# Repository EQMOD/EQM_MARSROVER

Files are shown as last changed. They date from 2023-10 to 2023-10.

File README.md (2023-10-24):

# EQM_MARSROVER
A 3d printed Mars Rover with DUAL Arduino Electronics

A 3D Printed Perseverance Mars Rover of NASA with dual Arduino Electronics.  The first Arduino a NANO, manages all 6 motors (speed and direction) of the 6-Wheel Rover where each wheel is independently controllable using the Arduino Servo libary. The motor speed controller uses the SG90 Servo board including the feedback potentiometer as an Electronic Speed Controller for each of the 6 wheels. Four more servo boards are added to manage the steering process performed on  all four corner wheels. So thats 6+4 SG90 Servo boards, 6 acting as Motor ESC and 4 as wheel steering. A 2nd BLE-33 Sense NANO Arduino with a TENSORFLOW AI/ML embedded engine  is used to process sensor data (built-in sensors within the Arduino, LIDARS, PIXYCAM, and MPU Gyro Sensor) The BLE-33 Sens NANO communicates with the 1st NANO Arduino via I2c. The entire platform is 3D-Printed with STL files downloaded from the NASA Website/GITHUB and were modified to accomodate the electronics and motors/servos. 

https://github.com/nasa/NASA-3D-Resources/tree/master/3D%20Models/M2020-Model-Rover-STLs512020



Rover Electronics mounted on the chassis box;



Sensor/Device List as implemented on the Arduino Codes;

"A TENSORFLOW AI/ML embedded module, 6 individually addressable bidirectional motors for all 6 Wheels, 4 LIDAR Sensors: two for the front two wheels, 1 at the rear wheel, 1 on the head mast, A CMU Pixy Camera mounted in front of the Rover, A streaming camera on the Main Mast accessible using wifi via a Mobile app, Dual Micro controllers in a master slave configuration,  two  6 DOF gyro/accelerometers - one on top of the differential bar, another on one on the Nano BLE Sense microcontroller, a light/color/proximity sensor on the ble sense, a barometric/temp/pressure also on the ble sense, an audio mic also on the ble sense, a couple of servos - one for the Mast, and one for the Ingenuity copter deployment, and FOUR more servos for each corner wheel, an RC module to remotely control the bot or feed it with PWM data for subroutine triggers  from the 2.4ghz transmitter , A Bluetooth module for mobile app communication..."

The platform also include a mini version of the Mars Ingenuity Helicopter to demonstrate the deployment process using a SG90 Servo to drop the model under the belly of the perseverance rover;



Ingenuity Deployment assembly  (Version 1)



Ingenuity Deployment assembly  (Version 2)



The Platform uses multiple sensors ((built-in sensors within the Arduino BLE Sense, LIDARS, PIXYCAM, and MPU Gyro Sensor) which can be used for multi-processing/interactive experiments



Below is the connection diagram of all the motors, servos, and sensors. Motor/Servo Control is distributed on the Arduino NANO (Acting as Slave) and the rest of the sensors including those connected to the I2C Bus are being controlled by the Arduino BLE-33 NANO Sense which is acting as the Master.  The Coring Motor (Rover Drill Motor) is connected to the BLE33 Sense as well the Servo Library Pins on the Arduino NANO side are fully utilized.



ARDUINO MASTER-SLAVE CONFIGURATION

The Arduninos operates in a master-slave configuration with the Master (NANO BLE Sense) defining 3 modes of operation;

Mode 1: RC Mode

        In this mode, control of the Rover is via a FLYSKY GT5 TX and FS-82 Receiver attached to the NANO Slave. The arduino NANO simply receives the channel info data from the transmitter via I-BUS connected to the Arduino RX pin and passes control to the Arduino Servo Library which performs the Motor/Servo control of the Rover.

Mode 2: RC with Sensor Mode

        In This mode, The Arduino NANO Slave cascades the FLYSKY Transmitter data to the NANO BLE Sense Master via I2C. The NANO BLE Sense Master then processes the transmitter data together with the sensor data attached to it and sends back to the NANO Slave the Motor/Servo control commands.
        
Mode 3: Autonomous Mode

        In this mode, there is no human intervention from the FLSKY Transmitter. Instead the Arduino BLE NANO Master reads the sensor data , decides on the what motor/servo commands to pass to the Arduino NANO Slave based on the information gathered from the sensors (LIDAR, PIXY, Audio, MPU6050 Gyro/Accelerometer, etc.



LIDARS and the CMU PIXY Camera

The platform has four LIDAR sensors and one CMU PIXY Camera for Visual Recognition



Two of the LIDAR Sensors are attached on each front wheel and one on the back wheel;



And another LIDAR sensor is located on the RSM Mast head side by side with a stand-alone wifi camera ;



A CMU PIXY Camera is attached on the front of the rover for realtime "front-of-rover" image analysis;



Arduino - PIXY CAMERA Processing



LIDAR and CMU Pixy Camera I2C BUS Addressing;

Anything attached on the I2C bus are addressable. The included code manages the pre-programming stuff of setting up the I2C address on the multiple LIDAR sensors so there will be no bus conflicts. Custom I2C Addresses are invidually re-assigned on three of the four LIDAR sensors connected on the same I2C bus. The way to do this is to put 3 of the LIDARS in reset
mode while the fourth one is assigned with a new address. Then one by one, the reset line of each is deactivated and assigned with a new address until all four will have unique i2c
addresses.



RC Electronics

The platform utlizes the FLYSKY TX-RX modules for receiving user command data from a FLYSKY FS-GT5 Transmitter and is received by the Ardruino Nano Slave via Flysky's I-BUS protocol which is directly fed to the Arduino NANO RX Pin.





Rover Wheels Geared Motors

Each wheel is driven independently by geared motors attaced on the bogie arm assembly.



The motor drivers are from the SG90 Servo boards acting as Electronic Speed Controllers with the feedback potentiometers adjusted for home position (where the motors stop rotating at TX / Steering wheel mid stick position)



Steering Servos. 

To reduce the space occupied by the servos, the SG90 servos where disassembled and the electronics attached to the 3d-printed bogie arm. The same Geared Motors on the wheels were used as motors for the servo arms.







3D Model of the Steering Servo mount to accomodate the SG90 Electronics plus a Potentiometer 3d printed  "Feed Back Pin" needed for the servo operation.



Potentiometer Feed Back Pin



The Arduino Slave Codes contain routines for an ACKERMAN STEERING and Turn-ON-Spot mode. This is user selectable
on the FLYSKY TX switch knobs or via a command from the Master Arduino BLE Sense side.





RSM Mast Servo 

The platform also includes a RSM Mast Servo for LIDAR and Wifi Camera Panning. The servo is located at the based 
of the RSM Mast Assembly



CORING DRILL MOTOR

The Rover Platform also has a Coring Drill Motor which is controllable from the Arduino Master side.



Perseverance Rover Platform Mount

For safekeeping a 3D Model of the platform mount is included;





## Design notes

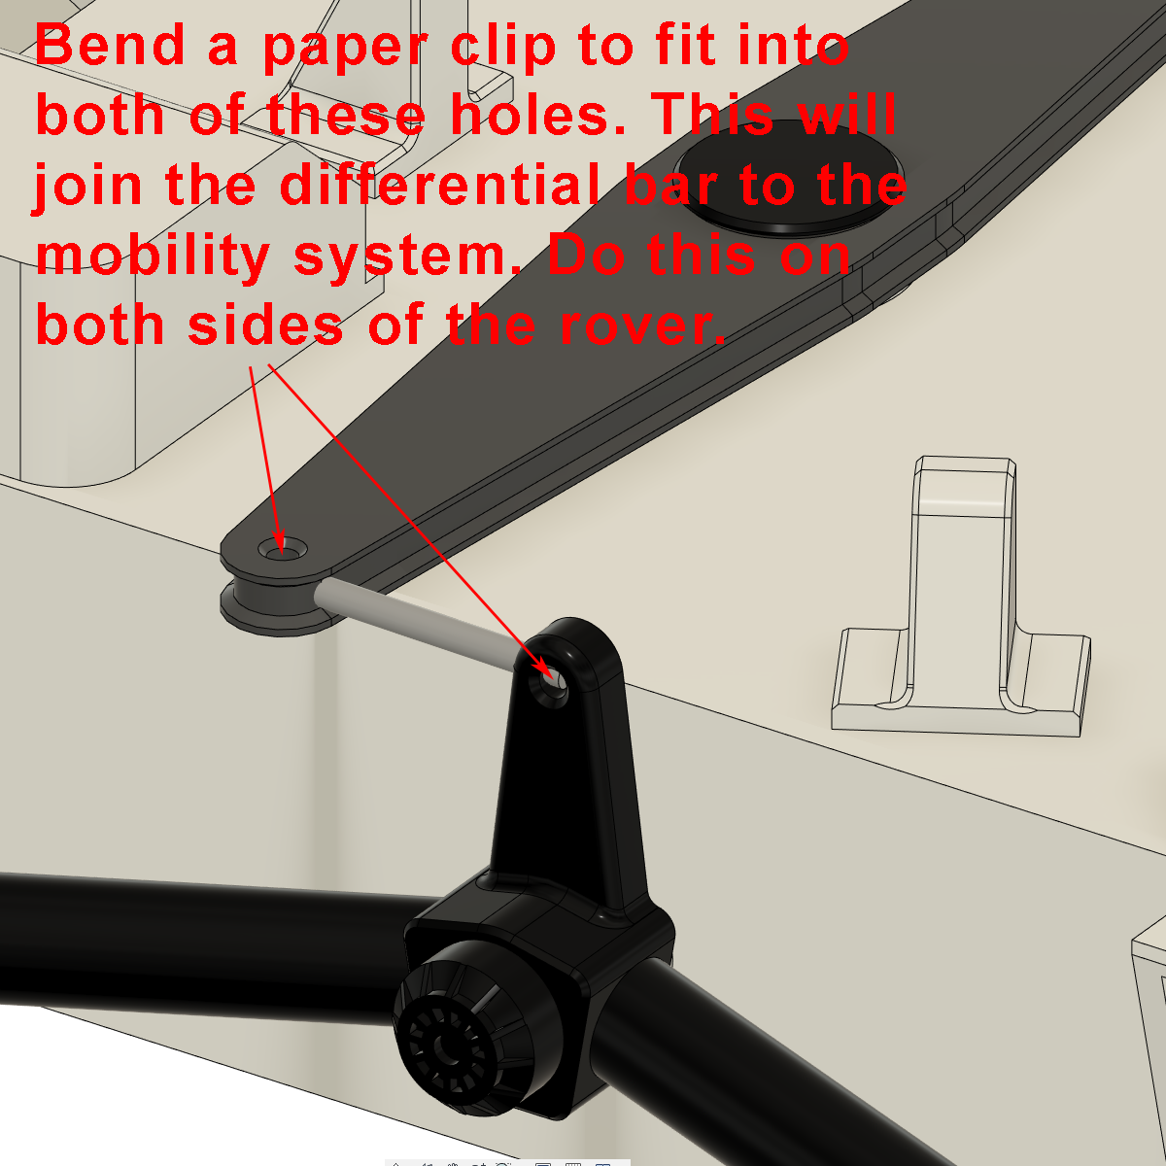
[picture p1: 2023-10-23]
3D Model Files/Instructions/differential_paperclip_bending.png

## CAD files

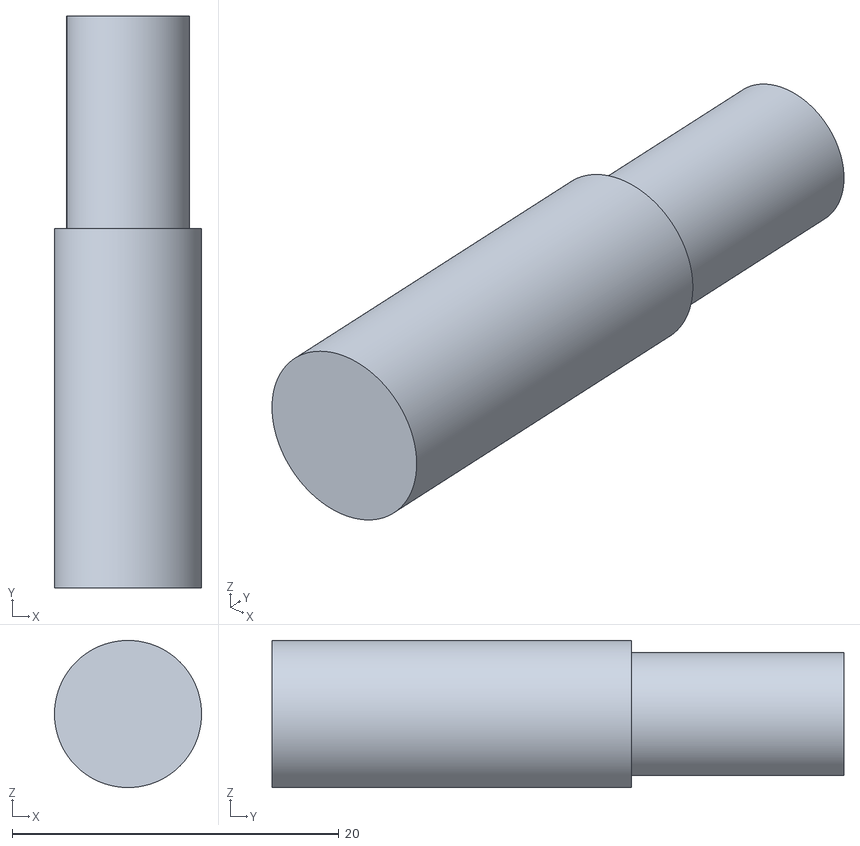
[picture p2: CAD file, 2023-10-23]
3D Model Files/STL_FILES/mobility_axle_pin.stl
9.00 x 35.0 x 9.00

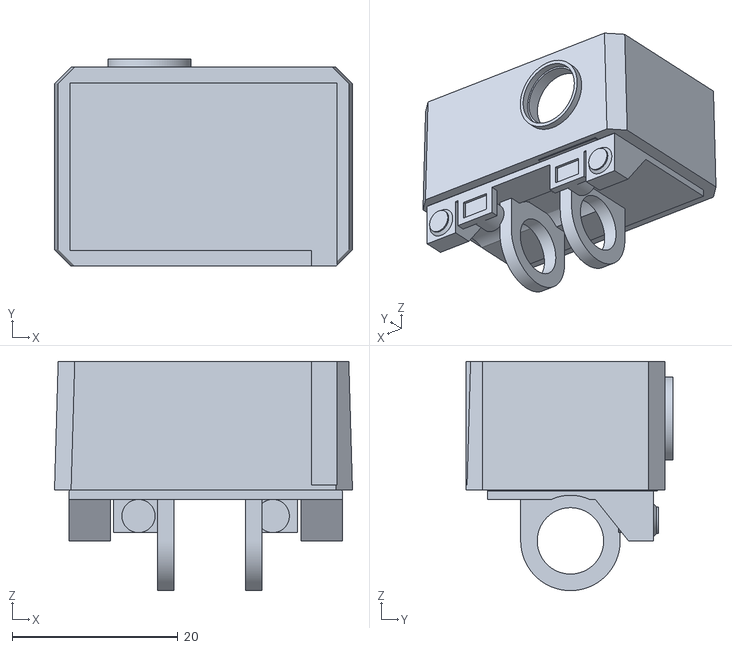
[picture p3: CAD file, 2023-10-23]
3D Model Files/STL_FILES/rsm_head2.stl
35.9 x 25.0 x 27.7

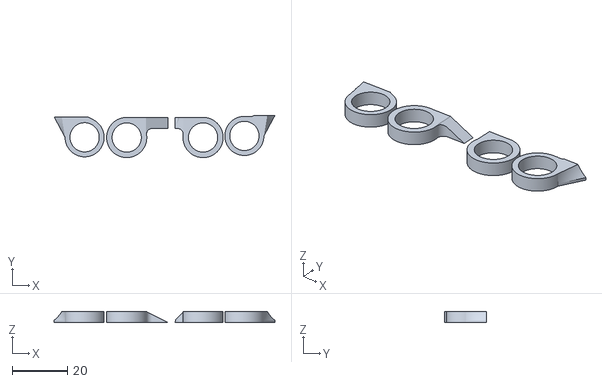
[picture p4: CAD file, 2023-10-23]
3D Model Files/STL_FILES/arm_turret_.stl
80.2 x 15.3 x 4.03

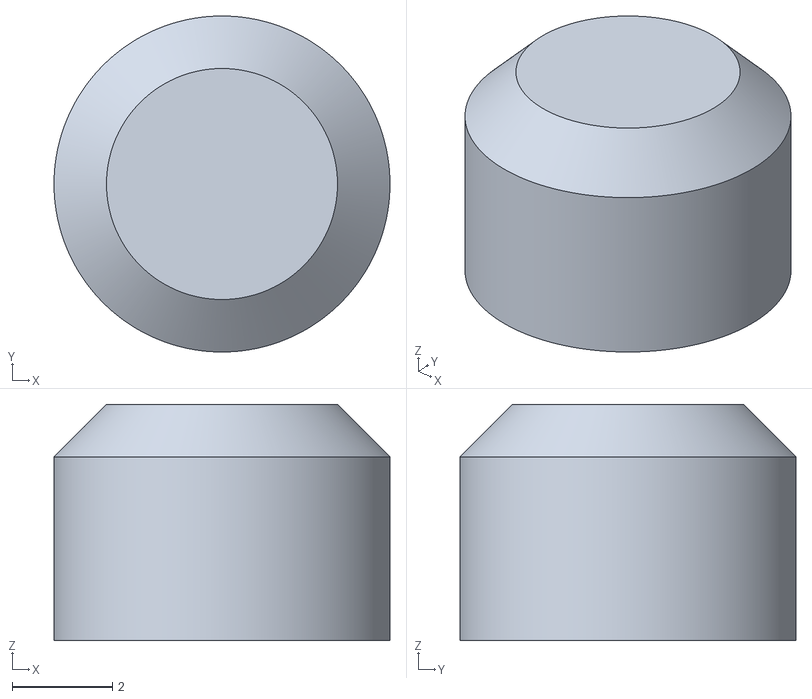
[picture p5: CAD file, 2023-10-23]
3D Model Files/STL_FILES/hga_antenna_cap.stl
6.72 x 6.72 x 4.72

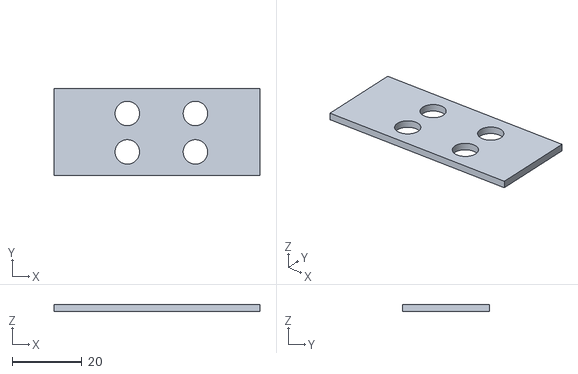
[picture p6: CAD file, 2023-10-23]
3D Model Files/STL_FILES/perse_batt_cover.stl
59.0 x 25.0 x 2.00

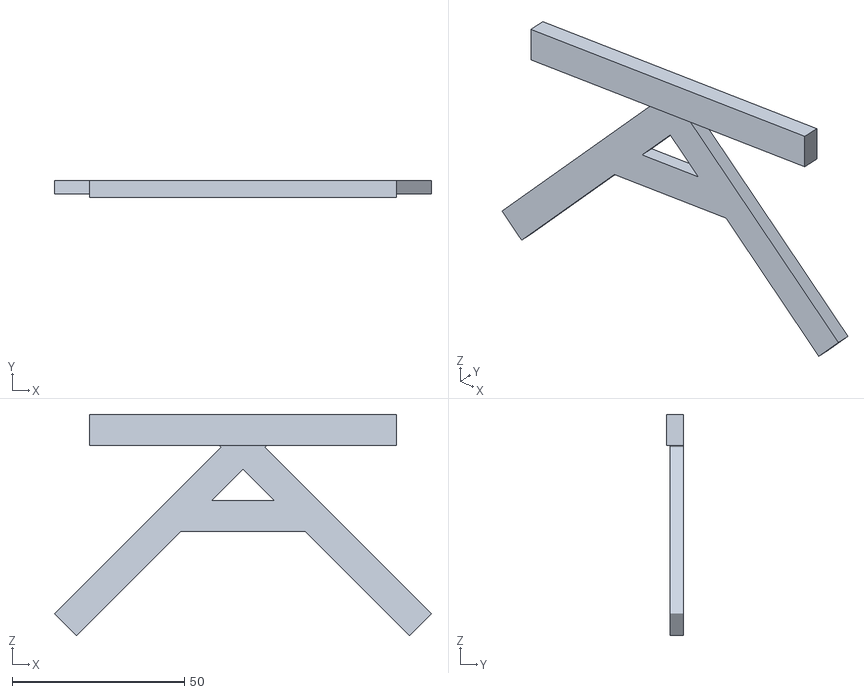
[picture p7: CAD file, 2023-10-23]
3D Model Files/STL_FILES/inge_platform_L4.stl
109.3 x 5.00 x 64.1

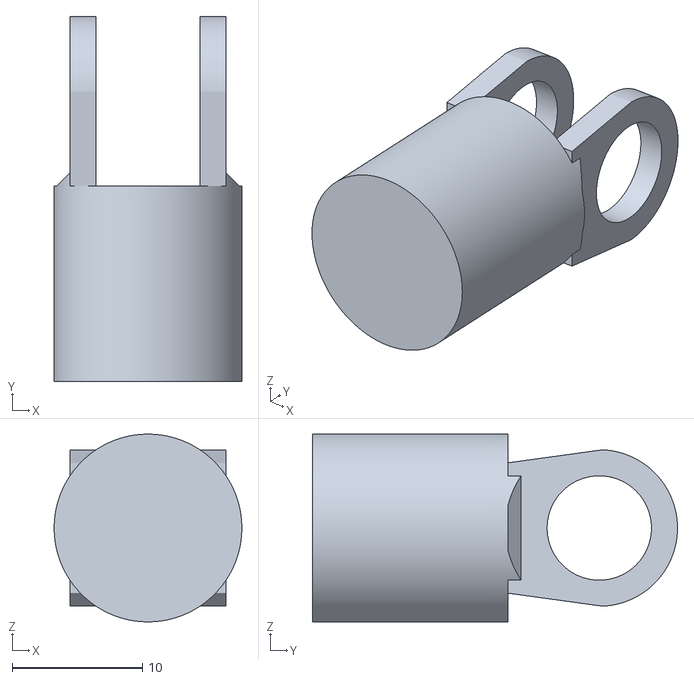
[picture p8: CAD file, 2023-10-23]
3D Model Files/STL_FILES/mars_2020_model_rsm_base.stl
14.4 x 28.0 x 14.4

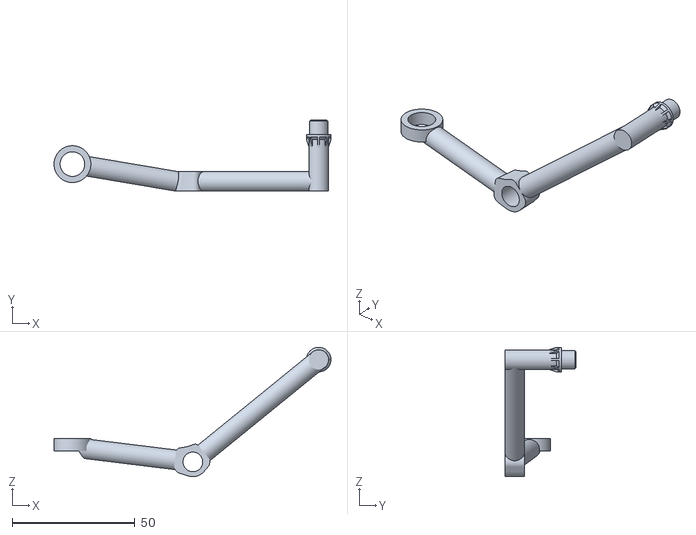
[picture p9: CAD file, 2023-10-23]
3D Model Files/STL_FILES/mobility_secondary_arm_right.stl
112.7 x 29.0 x 52.6

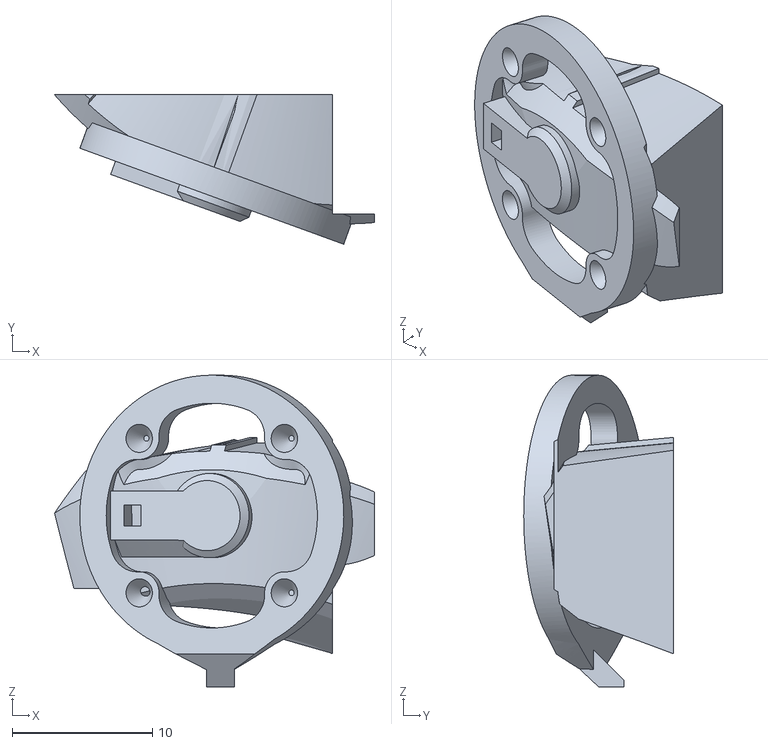
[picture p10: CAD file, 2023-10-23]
3D Model Files/STL_FILES/chasscircle.stl
22.8 x 10.6 x 22.2

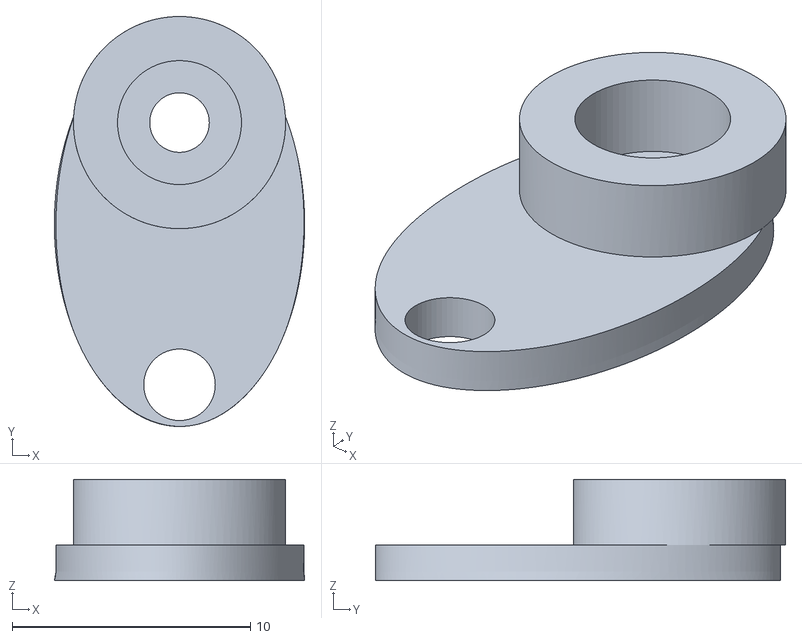
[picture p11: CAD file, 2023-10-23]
3D Model Files/STL_FILES/INGE_DEP_V2_SERVO_MAG2.stl
10.5 x 17.2 x 4.25

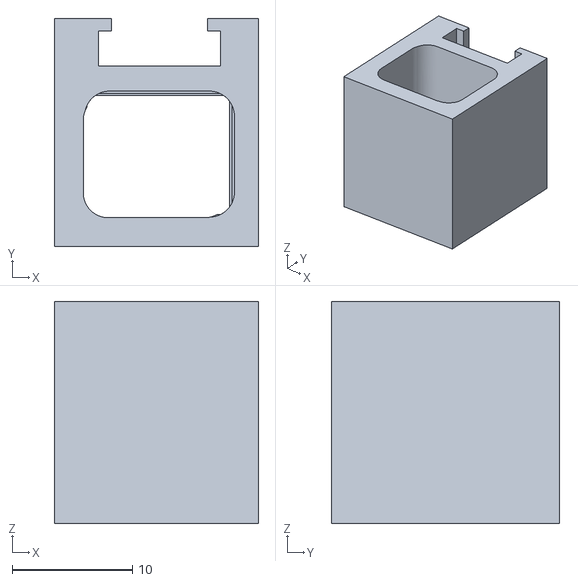
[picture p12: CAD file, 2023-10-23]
3D Model Files/STL_FILES/servolholder.stl
17.0 x 19.0 x 18.5

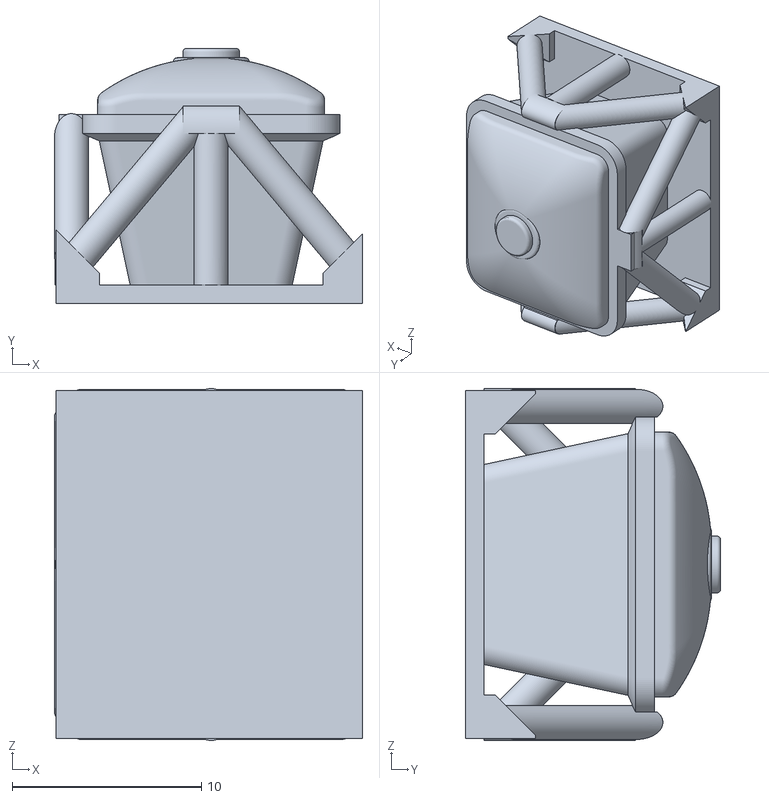
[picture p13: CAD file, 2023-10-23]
3D Model Files/STL_FILES/arm_turret_pixl.stl
16.3 x 13.5 x 18.6

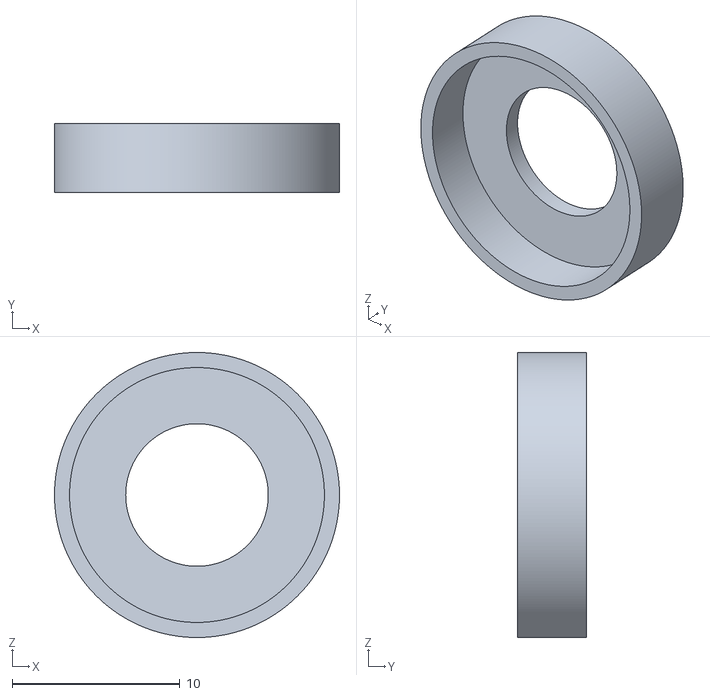
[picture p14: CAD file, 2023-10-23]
3D Model Files/STL_FILES/rsm_outer_ring.stl
17.0 x 4.10 x 17.0

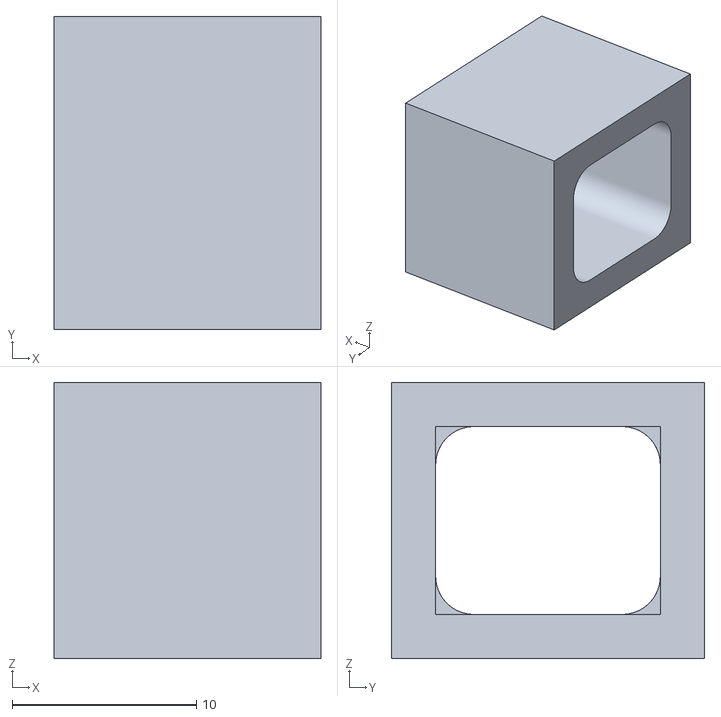
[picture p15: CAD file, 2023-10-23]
3D Model Files/STL_FILES/motor_v2.stl
14.5 x 17.0 x 15.0

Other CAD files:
3D Model Files/STL_FILES/arm_tube_2.stl
3D Model Files/STL_FILES/arm_turret_sherloc_watson.stl
3D Model Files/STL_FILES/prop1.stl
3D Model Files/STL_FILES/batcover_001.stl
3D Model Files/STL_FILES/INGE_DEP_V2_SERVO_MAG.stl
3D Model Files/STL_FILES/ardu_mount.stl
3D Model Files/STL_FILES/ardu_mount_cove2.stl
3D Model Files/STL_FILES/ardu_mount_cover.stl
3D Model Files/STL_FILES/arm_bracket_azimuth_elevation.stl
3D Model Files/STL_FILES/arm_bracket_wrist_turret.stl
3D Model Files/STL_FILES/arm_motor_cap.stl
3D Model Files/STL_FILES/arm_motor_mount.stl
3D Model Files/STL_FILES/arm_pin.stl
3D Model Files/STL_FILES/arm_pin_grovs.stl
3D Model Files/STL_FILES/arm_tube_1.stl
3D Model Files/STL_FILES/arm_turret_drill.stl
3D Model Files/STL_FILES/arm_turret_gdrt_fcs.stl
3D Model Files/STL_FILES/arm_turret_plate.stl
3D Model Files/STL_FILES/bATbOX_001.stl
3D Model Files/STL_FILES/box.stl
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

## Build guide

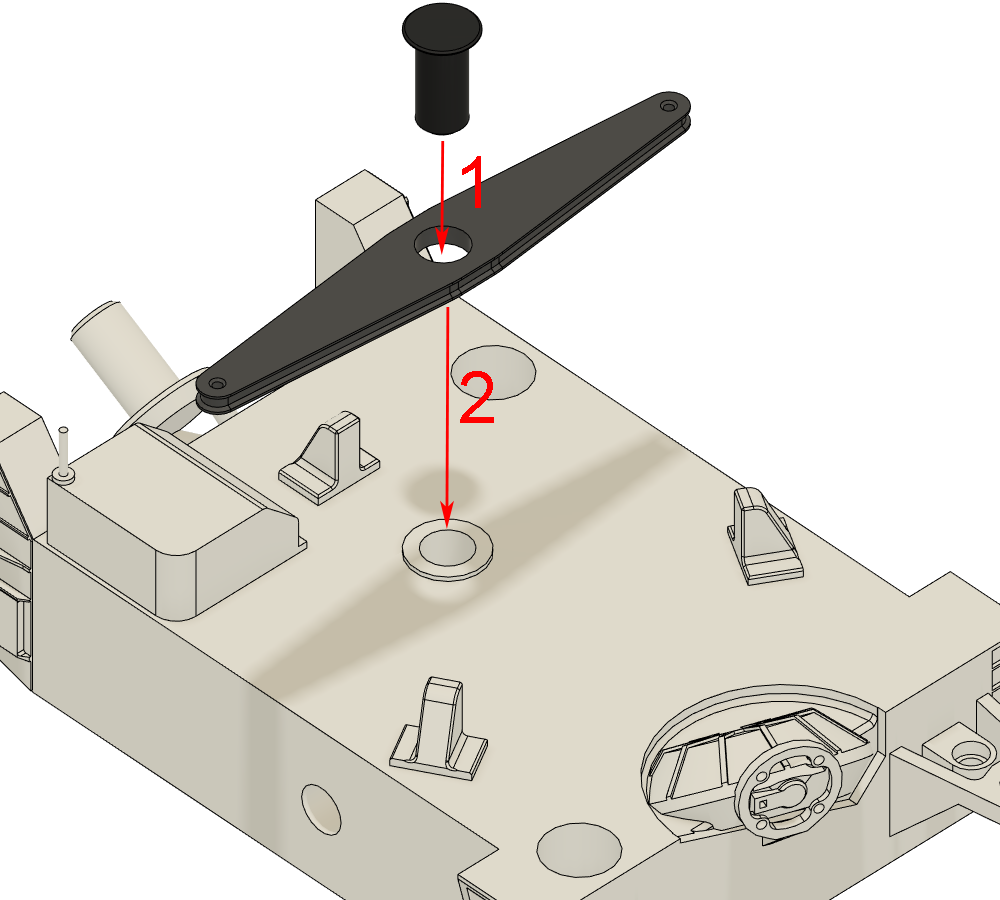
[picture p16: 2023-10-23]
3D Model Files/Instructions/differential_assembly.png

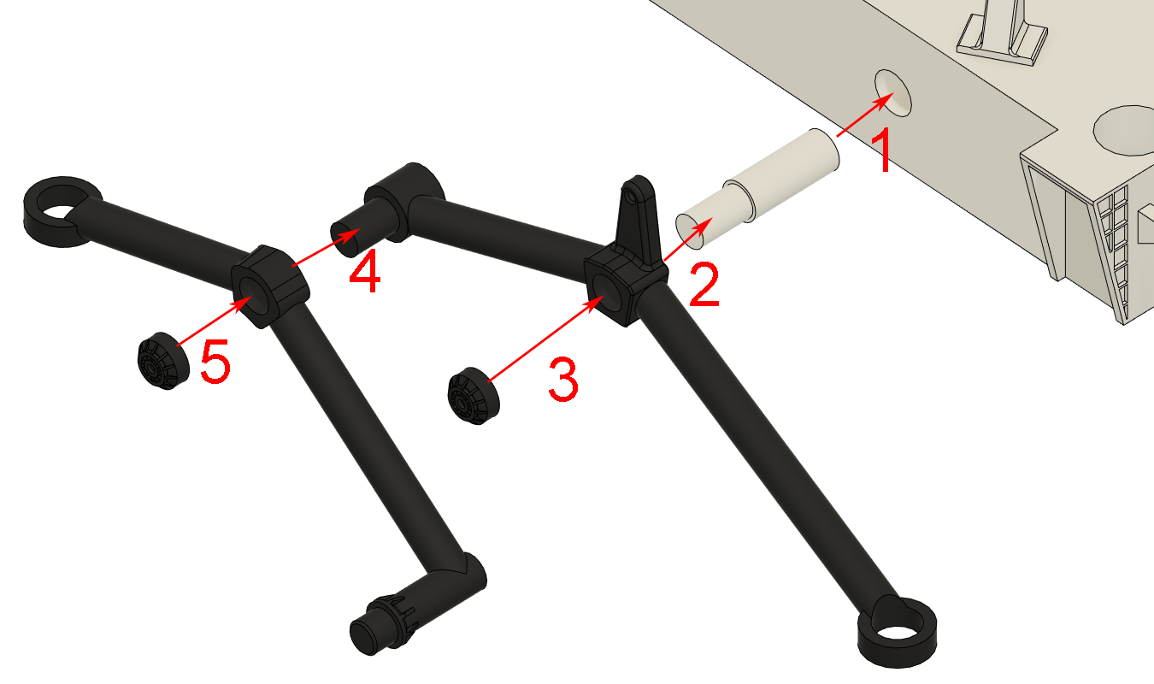
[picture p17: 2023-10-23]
3D Model Files/Instructions/mobility_arm_assembly.png

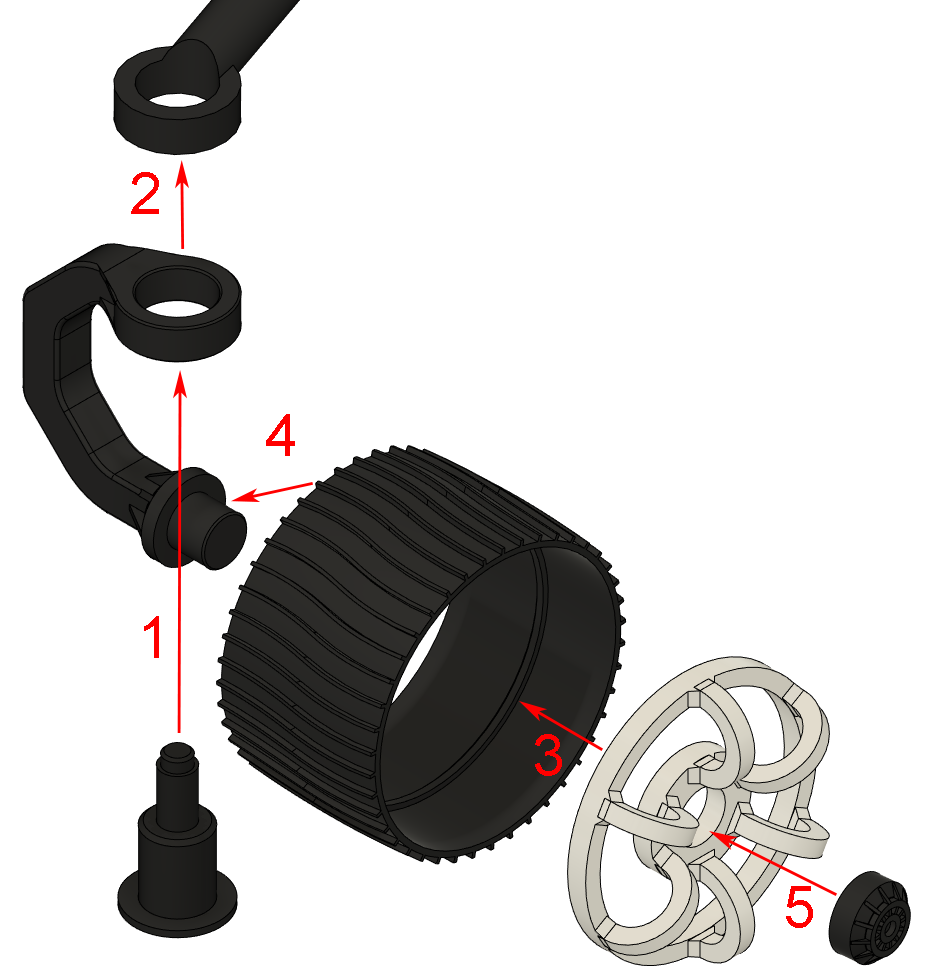
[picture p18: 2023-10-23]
3D Model Files/Instructions/wheel_assembly.png

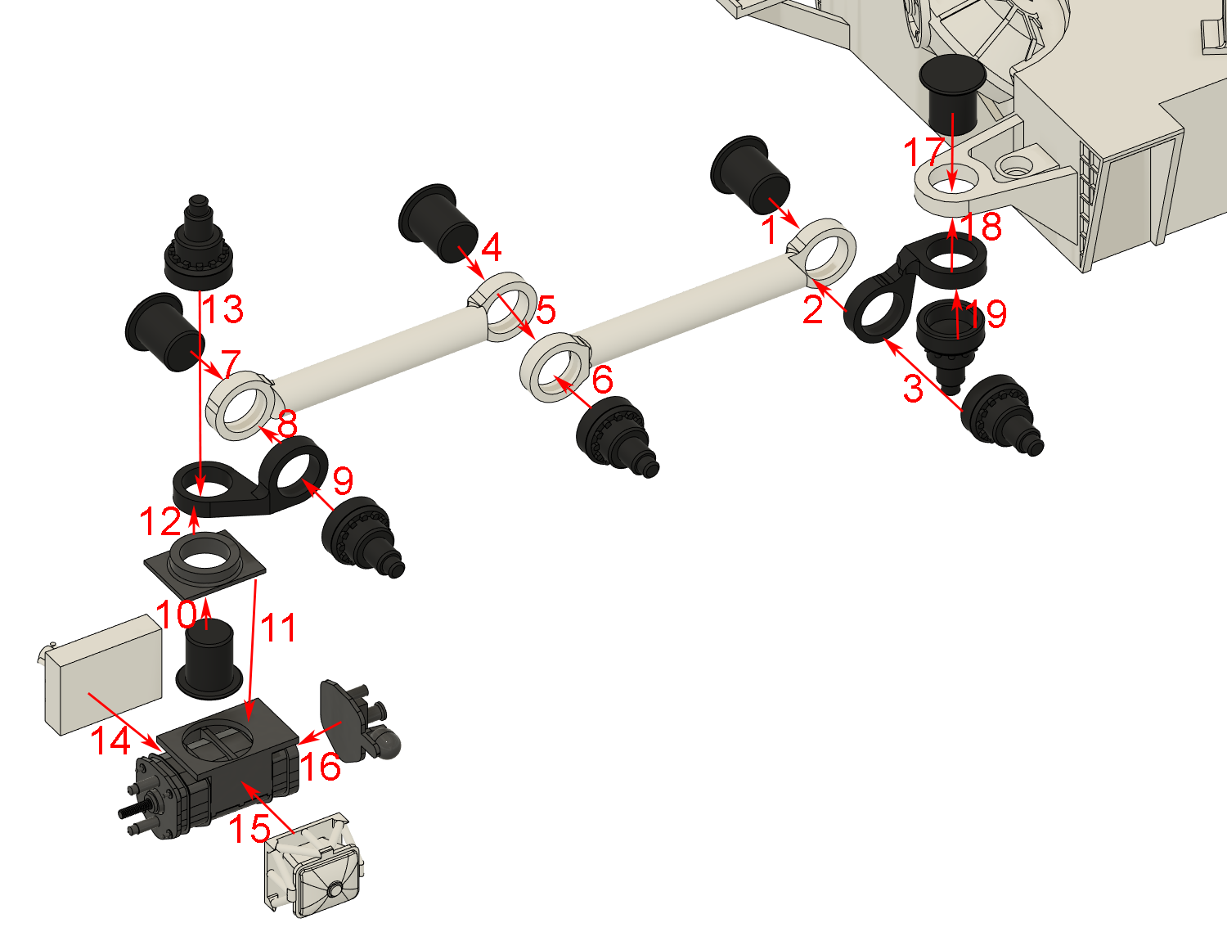
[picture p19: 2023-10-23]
3D Model Files/Instructions/robotic_arm_assembly.png

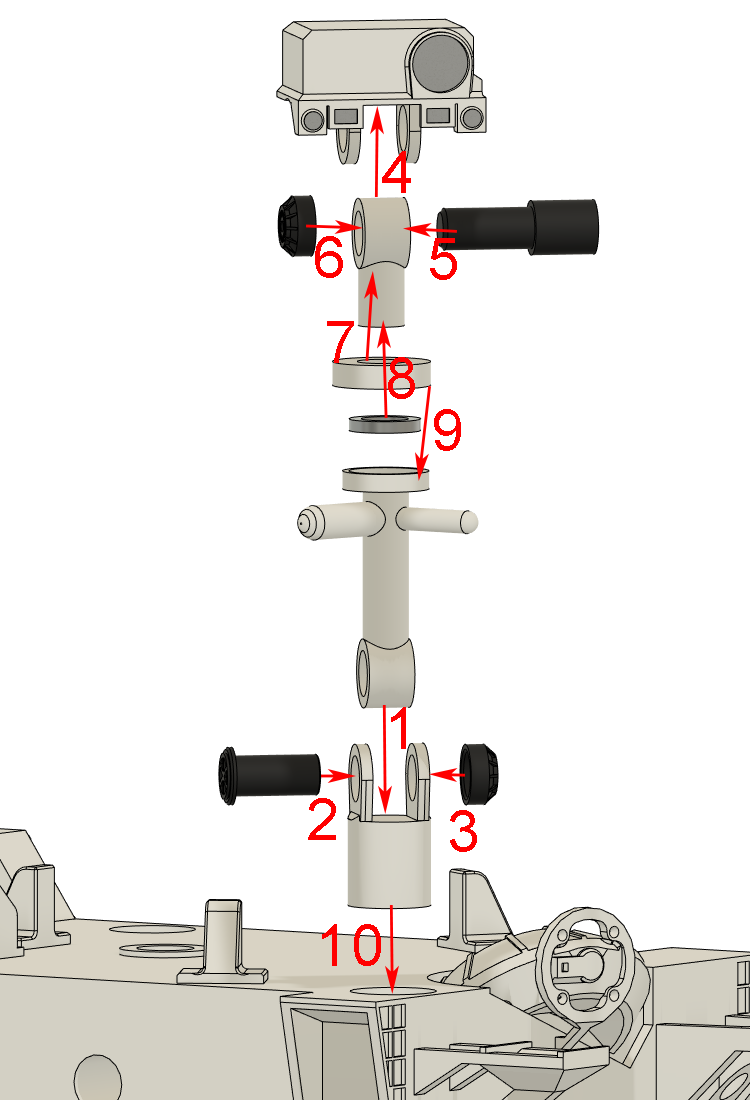
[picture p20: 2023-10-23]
3D Model Files/Instructions/rsm_assembly.png

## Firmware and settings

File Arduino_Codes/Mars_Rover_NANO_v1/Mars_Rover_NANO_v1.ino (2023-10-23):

//---------------------------------------------------------------------
// Copyright © 2020 Raymund Sarmiento
//
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
//  DISCLAIMER:

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
#include <Servo.h>
#include <ServoEasing.h>
#include <IBusBM.h>
#include <Wire.h>


ServoEasing Motor1;
ServoEasing Motor2;
ServoEasing Motor3;
ServoEasing Motor4;

ServoEasing Motor5;
ServoEasing Motor6;
ServoEasing Motor7;
ServoEasing Motor8;

ServoEasing Motor9;
ServoEasing Motor10;
ServoEasing ServoING;
ServoEasing ServoRSM;


Servo Motor11;




#define SRVFLOFST 100
#define SRVRLOFST 108
#define SRVFROFST 90
#define SRVRROFST 90

#define CoringNeutral 1593

#define AboveMid 1501
#define BelowMid 1499
#define AtMid   1500
#define AtMid1  1501

#define servomid 90

#define ppmrange 500
#define EPAHIGH  2000
#define EPALOW   1000

#define EPANEARHIGH 1800
#define EPANEARLOW 1300


#define TURNRADHIGH 500 
#define TURNRADLOW  120

#define POS1  1000
#define POS2  1500
#define POS3  2000

#define TOACTIVE 150 
#define SPFACTOR 4

IBusBM IBus;

int ch1, ch2, ch3, ch4, ch5, ch6,TXch1, TXch2, TXch3, TXch4, TXch5, TXch6, Pch1, Pch2, Pch3, Pch4, Pch5, Pch6 = 0;
int TXBypass = AtMid;
int motorspeed = 0; // rover speed
int steerradius = 0; // turning radius
int RawMode = AtMid;

int rearactive = 0;
int toactive_cnt = 0;
int sfactor = 0;

float spd1, spd2, spd3, spd1ppm, spd2ppm, spd3ppm, OuterFront, OuterBack, InnerFront, InnerBack = 0;


float CentertoCorner = 95;  
float CentertoRear = 98;
float CentertoFront = 100;
float CentertoMid = 100;


void setup() {

  sfactor = SPFACTOR;

  Serial.begin(115200);
  IBus.begin(Serial, IBUSBM_NOTIMER);    // iBUS object connected to serial0 RX pin

  pinMode(A0, INPUT);
  pinMode(A1, OUTPUT);
  pinMode(A2, OUTPUT);
  pinMode(A3, OUTPUT);

  digitalWrite(A1, LOW);
  digitalWrite(A2, LOW);
  digitalWrite(A3, LOW);

  Wire.begin(4);                // join i2c bus with address #8
  Wire.onRequest(requestEvent); // register event
  Wire.onReceive(receiveEvent); // register event
  
  // Wheel Motors
  
  Motor1.attach(2);  // Left Front Motor
  Motor2.attach(3);  // Lef Mid Motor
  Motor3.attach(4);  // Right Front Motor
  Motor4.attach(5);  // Right Mid Motor


  Motor9.attach(13); // Left Rear Motor
  Motor10.attach(10); // Rigth Rear Motor

  
  
  // Steering Motors 
  
  Motor5.attach(6);  // Front Left Steer Motor
  Motor6.attach(7);  // Rear Left Steer Motor
  Motor7.attach(8);  // Front Right Steer Motor
  Motor8.attach(9);  // Front Rear Steer Motor

  
 
  // Mast Servo 
  
  ServoRSM.attach(11);

   // Ingenuity Servo 
  
  ServoING.attach(12);


//Coring Drill

// Motor11.attach(A0);

  Motor1.writeMicroseconds(AtMid);
  Motor2.writeMicroseconds(AtMid);
  Motor3.writeMicroseconds(AtMid);
  Motor4.writeMicroseconds(AtMid);
  Motor9.writeMicroseconds(AtMid);
  Motor10.writeMicroseconds(AtMid);

  
  Motor5.write(SRVFLOFST);
  Motor6.write(SRVRLOFST);
  Motor7.write(SRVFROFST);
  Motor8.write(SRVRROFST);
  
  ServoRSM.write(servomid);
  ServoING.write(servomid);

 // Motor11.write(CoringNeutral);
 

  ch1 = AtMid;
  ch2 = AtMid;
  ch3 = AtMid;
  ch4 = POS1;
  ch5 = CoringNeutral;
  ch6 = AtMid;

  Pch1 = AtMid;
  Pch2 = AtMid;
  Pch3 = AtMid;
  Pch4 = POS1;
  Pch5 = CoringNeutral;
  Pch6 = AtMid;

  TXBypass = AtMid1;
  RawMode = AtMid;


}

void loop() {
  
  // read the TX data from the Ibus
  IBus.loop();
  
  TXch1 = IBus.readChannel(0);
  TXch2 = IBus.readChannel(1);
  TXch3 = IBus.readChannel(2);
  TXch4 = IBus.readChannel(3);
  TXch5 = IBus.readChannel(4);
  TXch6 = IBus.readChannel(5); 

  if (TXBypass == AtMid)
  {
      ch1 = TXch1;
      ch2 = TXch2;
      ch3 = TXch3;
      ch4 = TXch4;
      ch5 = TXch5;
      ch6 = TXch6;
  }


// Serial.print("ch1 ");Serial.print(ch1); Serial.print(" ch2 ");Serial.print(ch2);Serial.print(" ch6 ");Serial.print(ch6);Serial.print(" TxBypass ");Serial.println(TXBypass);


if (RawMode == AtMid)
{ 
if ((ch3 < AtMid) && (ch6 > EPAHIGH))
 rearactive = 1;
 else
  if (ch2 == AtMid)
  {
      toactive_cnt = TOACTIVE;
      rearactive = 0;
  }
  else
  {
      toactive_cnt--;
      if (toactive_cnt <= 0)
      {
        toactive_cnt = 0;
        rearactive = 1;
      }
  }

  // Right
  if (ch1 > AboveMid ) 
    steerradius = map(ch1, AboveMid, EPAHIGH, TURNRADHIGH, TURNRADLOW); 
  // left
  else if (ch1 < BelowMid) 
    steerradius = map(ch1, BelowMid, EPALOW, TURNRADHIGH, TURNRADLOW); 

  
  
  if (ch2 > AtMid)
    motorspeed = map(ch2, AtMid, EPAHIGH, 0, 100); // speed from 0% to 100%
  else if (ch2 < AtMid)
    motorspeed = map(ch2, AtMid, EPALOW, 0, 100); // speed from 0% to 100%
   else
      motorspeed = 0;
  
  GetMotorsSpeed();
  GetMotorAngle();

  // update ch3 data on Ingenuity Deploy Servo
  ServoING.writeMicroseconds(ch3); 

  // update ch6 data on RSM Mast Servo
  ServoRSM.writeMicroseconds(ch6);

  // update Cording drill Motor data 
  //if (ch5 != 0)
    //  Motor11.writeMicroseconds(ch5);
  //else
    //  Motor11.writeMicroseconds(CoringNeutral);  // Make sure Drill Motor is not active in the absence of an RX

  switch (ch4)
  
  {
    
    case POS1:
  
          // right
          if (ch1 > AboveMid) {
          // Corner Steering Motors
          Motor7.write(SRVFROFST + InnerFront); 
          Motor8.write(SRVRROFST - InnerBack); 
          Motor5.write(SRVFLOFST + OuterFront); 
          Motor6.write(SRVRLOFST - OuterBack); 

          // Set speed of all wheel motors
          if (ch2 > AtMid) // Forward
          { 
            Motor1.writeMicroseconds(AtMid + spd1ppm);
            Motor2.writeMicroseconds(AtMid + spd1ppm);
            Motor3.writeMicroseconds(AtMid + spd2ppm);
            Motor4.writeMicroseconds(AtMid + spd3ppm);

            if (rearactive == 1)
            {
                Motor9.writeMicroseconds(AtMid + spd1ppm);
                Motor10.writeMicroseconds(AtMid + spd2ppm);
            }
            else
            {
                Motor9.writeMicroseconds(AtMid + (spd1ppm/sfactor));
                Motor10.writeMicroseconds(AtMid + (spd2ppm/sfactor));
            }
            
          }
          else if (ch2 < AtMid) // Reverse
          {
            Motor1.writeMicroseconds(AtMid - spd1ppm);
            Motor2.writeMicroseconds(AtMid - spd1ppm);
            Motor3.writeMicroseconds(AtMid - spd2ppm);
            Motor4.writeMicroseconds(AtMid - spd3ppm);

            if (rearactive == 1)
            {
                Motor9.writeMicroseconds(AtMid - spd1ppm);
                Motor10.writeMicroseconds(AtMid - spd2ppm);
            }            
            else
            {
                Motor9.writeMicroseconds(AtMid - (spd1ppm/sfactor));
                Motor10.writeMicroseconds(AtMid - (spd2ppm/sfactor));
            }
            
          }
          else  // At Rest
          {
            Motor1.writeMicroseconds(ch2);
            Motor2.writeMicroseconds(ch2);
            Motor3.writeMicroseconds(ch2);
            Motor4.writeMicroseconds(ch2);

            if (rearactive == 1)
            {
                Motor9.writeMicroseconds(ch2);
                Motor10.writeMicroseconds(ch2);
            }
            else
            {

               if (ch2 > AtMid)
               {
                   Motor9.writeMicroseconds(AtMid+((ch2-AtMid)/sfactor));
                   Motor10.writeMicroseconds(AtMid+((ch2-AtMid)/sfactor));
               }
               else
               {
                   Motor9.writeMicroseconds(AtMid-((AtMid-ch2)/sfactor));
                   Motor10.writeMicroseconds(AtMid-((AtMid-ch2)/sfactor));
               }
               
            }

          }

          }

          // left
          else if (ch1 < BelowMid) {
          // Corner Steering motors
          Motor7.write(SRVFROFST - OuterFront);
          Motor8.write(SRVRROFST + OuterBack);
          Motor5.write(SRVFLOFST - InnerFront);
          Motor6.write(SRVRLOFST + InnerBack);

          if (ch2 > AtMid) // Forward
          { 
            Motor1.writeMicroseconds(AtMid + spd2ppm);
            Motor2.writeMicroseconds(AtMid + spd3ppm);
            Motor3.writeMicroseconds(AtMid + spd1ppm);
            Motor4.writeMicroseconds(AtMid + spd1ppm);

            if (rearactive == 1)
            {
                Motor9.writeMicroseconds(AtMid + spd2ppm);
                Motor10.writeMicroseconds(AtMid + spd1ppm);
            }          
            else
            {
                Motor9.writeMicroseconds(AtMid + (spd2ppm/sfactor));
                Motor10.writeMicroseconds(AtMid + (spd1ppm/sfactor));
            }
          
          }
          else if (ch2 < AtMid) // Reverse
          { 
            Motor1.writeMicroseconds(AtMid - spd2ppm);
            Motor2.writeMicroseconds(AtMid - spd3ppm);
            Motor3.writeMicroseconds(AtMid - spd1ppm);
            Motor4.writeMicroseconds(AtMid - spd1ppm);

            if (rearactive == 1)
            {
                Motor9.writeMicroseconds(AtMid - spd2ppm);
                Motor10.writeMicroseconds(AtMid - spd1ppm);
            }
            else
            {
                Motor9.writeMicroseconds(AtMid - (spd2ppm/sfactor));
                Motor10.writeMicroseconds(AtMid - (spd1ppm/sfactor));
            }
          
          }
          else
          {
            Motor1.writeMicroseconds(ch2);
            Motor2.writeMicroseconds(ch2);
            Motor3.writeMicroseconds(ch2);
            Motor4.writeMicroseconds(ch2);

            if (rearactive == 1)
            {
                Motor9.writeMicroseconds(ch2);
                Motor10.writeMicroseconds(ch2);
            }
            else
            {
               if (ch2 > AtMid)
               {
                   Motor9.writeMicroseconds(AtMid+((ch2-AtMid)/sfactor));
                   Motor10.writeMicroseconds(AtMid+((ch2-AtMid)/sfactor));
               }
               else
               {
                   Motor9.writeMicroseconds(AtMid-((AtMid-ch2)/sfactor));
                   Motor10.writeMicroseconds(AtMid-((AtMid-ch2)/sfactor));
               }
            }
          
          }

          }

          else {

            // Straight driving (throttle only)
  
            Motor1.writeMicroseconds(ch2);
            Motor2.writeMicroseconds(ch2);
            Motor3.writeMicroseconds(ch2);
            Motor4.writeMicroseconds(ch2);

            if (rearactive == 1)
            {
                Motor9.writeMicroseconds(ch2);
                Motor10.writeMicroseconds(ch2);
            }
            else
            {
               if (ch2 > AtMid)
               {
                   Motor9.writeMicroseconds(AtMid+((ch2-AtMid)/sfactor));
                   Motor10.writeMicroseconds(AtMid+((ch2-AtMid)/sfactor));
               }
               else
               {
                   Motor9.writeMicroseconds(AtMid-((AtMid-ch2)/sfactor));
                   Motor10.writeMicroseconds(AtMid-((AtMid-ch2)/sfactor));
               }
            }
  
            // Corner Steering Motors in straight position
  
            Motor5.write(SRVFLOFST);
            Motor6.write(SRVRLOFST);
            Motor7.write(SRVFROFST);
            Motor8.write(SRVRROFST);

            }

          
          
          break;
    
    case POS2:    


          // Corner Steering Motors
          if  ((ch1 > AboveMid) ||  (ch1 < BelowMid))
          {
            Motor7.write(SRVFROFST - (InnerFront/2)); // front wheel steer right
            Motor8.write(SRVRROFST + (InnerBack/2)); // back wheel steer left for overall steering to the right of the rover
            Motor5.write(SRVFLOFST + (InnerFront/2)); // front wheel steer right
            Motor6.write(SRVRLOFST - (InnerBack/2)); // back wheel steer left for overall steering to the right of the rover
          }
          else
          {
            Motor5.write(SRVFLOFST);
            Motor6.write(SRVRLOFST);
            Motor7.write(SRVFROFST);
            Motor8.write(SRVRROFST);

          }


          if (ch1 > EPANEARHIGH)
          {
            // Set speed of all wheel motors
            if (ch2 > AtMid) // Forward
            { 
              Motor1.writeMicroseconds(AtMid + spd1ppm);
              Motor2.writeMicroseconds(AtMid + spd1ppm);
              Motor3.writeMicroseconds(AtMid - spd1ppm);
              Motor4.writeMicroseconds(AtMid - spd1ppm);

              Motor9.writeMicroseconds(AtMid + spd1ppm);
              Motor10.writeMicroseconds(AtMid - spd1ppm);
            
            
            }
            else if (ch2 < AtMid) // Reverse
            {
              Motor1.writeMicroseconds(AtMid - spd1ppm);
              Motor2.writeMicroseconds(AtMid - spd1ppm);
              Motor3.writeMicroseconds(AtMid + spd1ppm);
              Motor4.writeMicroseconds(AtMid + spd1ppm);

              Motor9.writeMicroseconds(AtMid - spd1ppm);
              Motor10.writeMicroseconds(AtMid + spd1ppm);
            
            
            }
            else  // At Rest
            {
              Motor1.writeMicroseconds(ch2);
              Motor2.writeMicroseconds(ch2);
              Motor3.writeMicroseconds(ch2);
              Motor4.writeMicroseconds(ch2);

              Motor9.writeMicroseconds(ch2);
              Motor10.writeMicroseconds(ch2);
            
            }
          }
          else
          if (ch1 < EPANEARLOW)
          {
            // Set speed of all wheel motors
            if (ch2 > AtMid) // Forward
            { 
              Motor1.writeMicroseconds(AtMid - spd1ppm);
              Motor2.writeMicroseconds(AtMid - spd1ppm);
              Motor3.writeMicroseconds(AtMid + spd1ppm);
              Motor4.writeMicroseconds(AtMid + spd1ppm);

              Motor9.writeMicroseconds(AtMid - spd1ppm);
              Motor10.writeMicroseconds(AtMid + spd1ppm);
            
            }
            else if (ch2 < AtMid) // Reverse
            {
              Motor1.writeMicroseconds(AtMid + spd1ppm);
              Motor2.writeMicroseconds(AtMid + spd1ppm);
              Motor3.writeMicroseconds(AtMid - spd1ppm);
              Motor4.writeMicroseconds(AtMid - spd1ppm);

              Motor9.writeMicroseconds(AtMid + spd1ppm);
              Motor10.writeMicroseconds(AtMid - spd1ppm);
            
            }
            else  // At Rest
            {
              Motor1.writeMicroseconds(ch2);
              Motor2.writeMicroseconds(ch2);
              Motor3.writeMicroseconds(ch2);
              Motor4.writeMicroseconds(ch2);

              Motor9.writeMicroseconds(ch2);
              Motor10.writeMicroseconds(ch2);
            
            }
          }
          else
          {
              Motor1.writeMicroseconds(ch2);
              Motor2.writeMicroseconds(ch2);
              Motor3.writeMicroseconds(ch2);
              Motor4.writeMicroseconds(ch2);          

              Motor9.writeMicroseconds(ch2);
              Motor10.writeMicroseconds(ch2);
          
          }
          break;
    default:

// check if testmode

        if ((ch3 < AtMid) && (ch6 > EPAHIGH))
        {
            // TESTMODE CH4 POS3, CH3 LOCK, CH6 PAN LEFT

            if ((ch5>=1000) && (ch5 < 1100)) Motor1.writeMicroseconds(ch2);
            else if ((ch5>=1100) && (ch5 < 1200)) Motor2.writeMicroseconds(ch2);
            else if ((ch5>=1200) && (ch5 < 1300)) Motor9.writeMicroseconds(ch2);
            else if ((ch5>=1300) && (ch5 < 1400)) Motor3.writeMicroseconds(ch2);
            else if ((ch5>=1400) && (ch5 < 1500)) Motor4.writeMicroseconds(ch2);
            else if ((ch5>=1500) && (ch5 < 1600)) Motor10.writeMicroseconds(ch2);
            else if ((ch5>=1600) && (ch5 < 1700)) Motor5.writeMicroseconds(ch2);
            else if ((ch5>=1700) && (ch5 < 1800)) Motor6.writeMicroseconds(ch2);
            else if ((ch5>=1800) && (ch5 < 1900)) Motor7.writeMicroseconds(ch2);
            else  Motor8.writeMicroseconds(ch2);

        }
        else
        {
        if ((ch2 < AboveMid) &&  (ch2 > BelowMid)) 
        {
          if  ((ch1 > AboveMid) ||  (ch1 < BelowMid))
          {
            Motor7.write(SRVFROFST - (InnerFront/2)); // front wheel steer right
            Motor8.write(SRVRROFST + (InnerBack/2)); // back wheel steer left for overall steering to the right of the rover
            Motor5.write(SRVFLOFST + (InnerFront/2)); // front wheel steer right
            Motor6.write(SRVRLOFST - (InnerBack/2)); // back wheel steer left for overall steering to the right of the rover
          }
          else
          {
            Motor5.write(SRVFLOFST);
            Motor6.write(SRVRLOFST);
            Motor7.write(SRVFROFST);
            Motor8.write(SRVRROFST);

          }
          
          if ((ch1 > EPANEARHIGH)|| (ch1 < EPANEARLOW))
          {
              Motor1.writeMicroseconds(ch1);
              Motor2.writeMicroseconds(ch1);
              Motor3.writeMicroseconds(AtMid - (ch1 - AtMid));
              Motor4.writeMicroseconds(AtMid - (ch1 - AtMid));

              Motor9.writeMicroseconds(ch1);
              Motor10.writeMicroseconds(AtMid - (ch1 - AtMid));
          
          }
          else
          {
              Motor1.writeMicroseconds(ch2);
              Motor2.writeMicroseconds(ch2);
              Motor3.writeMicroseconds(ch2);
              Motor4.writeMicroseconds(ch2);          

              Motor9.writeMicroseconds(ch2);
              Motor10.writeMicroseconds(ch2);
          
          }


          
        }
        else
        {
          // right
          if (ch1 > AboveMid) {
          // Corner Steering Motors
          Motor7.write(SRVFROFST + InnerFront); // front wheel steer right
          Motor8.write(SRVRROFST - InnerBack); // back wheel steer left for overall steering to the right of the rover
          Motor5.write(SRVFLOFST + OuterFront); // front wheel steer right
          Motor6.write(SRVRLOFST - OuterBack); // back wheel steer left for overall steering to the right of the rover

          // Set speed of all wheel motors
          if (ch2 > AtMid) // Forward
          { 
            Motor1.writeMicroseconds(AtMid + spd1ppm);
            Motor2.writeMicroseconds(AtMid + spd1ppm);
            Motor3.writeMicroseconds(AtMid + spd2ppm);
            Motor4.writeMicroseconds(AtMid + spd3ppm);

            Motor9.writeMicroseconds(AtMid + spd1ppm);
            Motor10.writeMicroseconds(AtMid + spd2ppm);
          
          }
          else if (ch2 < AtMid) // Reverse
          {
            Motor1.writeMicroseconds(AtMid - spd1ppm);
            Motor2.writeMicroseconds(AtMid - spd1ppm);
            Motor3.writeMicroseconds(AtMid - spd2ppm);
            Motor4.writeMicroseconds(AtMid - spd3ppm);

            Motor9.writeMicroseconds(AtMid - spd1ppm);
            Motor10.writeMicroseconds(AtMid - spd2ppm);

          
          }
          else  // At Rest
          {
            Motor1.writeMicroseconds(ch2);
            Motor2.writeMicroseconds(ch2);
            Motor3.writeMicroseconds(ch2);
            Motor4.writeMicroseconds(ch2);

            Motor9.writeMicroseconds(ch2);
            Motor10.writeMicroseconds(ch2);

          
          }

          }

          // left
          else if (ch1 < BelowMid) {
          // Corner Steering motors
          Motor7.write(SRVFROFST - OuterFront);
          Motor8.write(SRVRROFST + OuterBack);
          Motor5.write(SRVFLOFST - InnerFront);
          Motor6.write(SRVRLOFST + InnerBack);

          if (ch2 > AtMid) // Forward
          { 
            Motor1.writeMicroseconds(AtMid + spd2ppm);
            Motor2.writeMicroseconds(AtMid + spd3ppm);
            Motor3.writeMicroseconds(AtMid + spd1ppm);
            Motor4.writeMicroseconds(AtMid + spd1ppm);

            Motor9.writeMicroseconds(AtMid + spd2ppm);
            Motor10.writeMicroseconds(AtMid + spd1ppm);
          
          }
          else if (ch2 < AtMid) // Reverse
          { 
            Motor1.writeMicroseconds(AtMid - spd2ppm);
            Motor2.writeMicroseconds(AtMid - spd3ppm);
            Motor3.writeMicroseconds(AtMid - spd1ppm);
            Motor4.writeMicroseconds(AtMid - spd1ppm);

            Motor9.writeMicroseconds(AtMid - spd2ppm);
            Motor10.writeMicroseconds(AtMid - spd1ppm);

          }
          else
          {
            Motor1.writeMicroseconds(ch2);
            Motor2.writeMicroseconds(ch2);
            Motor3.writeMicroseconds(ch2);
            Motor4.writeMicroseconds(ch2);

            Motor9.writeMicroseconds(ch2);
            Motor10.writeMicroseconds(ch2);
          
          }

          }

          else {

            // Straight driving (throttle only)
  
            Motor1.writeMicroseconds(ch2);
            Motor2.writeMicroseconds(ch2);
            Motor3.writeMicroseconds(ch2);
            Motor4.writeMicroseconds(ch2);

            Motor9.writeMicroseconds(ch2);
            Motor10.writeMicroseconds(ch2);

  
            // Corner Steering Motors in straight position
  
            Motor5.write(SRVFLOFST);
            Motor6.write(SRVRLOFST);
            Motor7.write(SRVFROFST);
            Motor8.write(SRVRROFST);

            }

        } 
        }  
          break;
        
  }

} // Rawmode
}
void GetMotorsSpeed() {
  // if no steering, all wheels speed is the same - straight move
  if (ch1 == AtMid) {
    spd1 = spd2 = spd3 = motorspeed;
  }

  else {
    spd1 = motorspeed;
    spd2 = motorspeed * sqrt(pow(CentertoFront, 2) + 
       pow((steerradius - CentertoCorner), 2)) / 
       (steerradius + CentertoMid);
    spd3 = motorspeed * (steerradius - CentertoMid) / 
  (steerradius + CentertoMid);
  }

  spd1ppm = map(round(spd1), 0, 100, 0, ppmrange);
  spd2ppm = map(round(spd2), 0, 100, 0, ppmrange);
  spd3ppm = map(round(spd3), 0, 100, 0, ppmrange);
}
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

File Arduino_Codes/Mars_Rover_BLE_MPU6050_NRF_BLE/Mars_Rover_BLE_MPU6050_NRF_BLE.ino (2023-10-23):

//---------------------------------------------------------------------
// Copyright © 2020 Raymund Sarmiento
//
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
//  DISCLAIMER:

//  You can use the information on this site COMPLETELY AT YOUR OWN RISK.
//  The modification steps and other information on this site is provided
//  to you "AS IS" and WITHOUT WARRANTY OF ANY KIND, express, statutory,
//  implied or otherwise, including without limitation any warranty of
//  merchantability or fitness for any particular or intended purpose.
//  In no event the author will  be liable for any direct, indirect,
//  punitive, special, incidental or consequential damages or loss of any
//  kind whether or not the author  has been advised of the possibility
//  of such loss.
//---------------------------------------------------------------------
#include <Wire.h>
#include <Servo.h>

#include <Adafruit_MPU6050.h>
#include <Adafruit_Sensor.h>

#include <HardwareBLESerial.h>

HardwareBLESerial &bleSerial = HardwareBLESerial::getInstance();

#define TIMER_INTERRUPT_DEBUG         0
#define _TIMERINTERRUPT_LOGLEVEL_     0

#include "NRF52_MBED_TimerInterrupt.h"

#include "NRF52_MBED_ISR_Timer.h"

NRF52_MBED_Timer ITimer(NRF_TIMER_3);

// Init NRF52_MBED_ISRTimer
// Each NRF52_MBED_ISRTimer can service 16 different ISR-based timers
NRF52_MBED_ISRTimer ISR_Timer;

#define TIMER_INTERVAL_100mS             100L
#define HW_TIMER_INTERVAL_MS      1

void TimerHandler()
{
  ISR_Timer.run();
}


Adafruit_MPU6050 mpu;

Servo Motor11;

#define MPU_INT0 D2
#define AboveMid 1501
#define BelowMid 1499
#define AtMid   1500
#define AtMid1  1501
#define AtStart 1000
#define AtEnd 2000

#define DEFGAIN  90
#define PWMMULTIP 50
#define INGENDEPDELAY 1000    // Deployment Servo return delay in ms
#define INGENOFFSET 100
#define GYROSTABILIZEDELAY 20  // Routine delay for 2 secs (multiple of 100 ms)
#define DEFDURATION 1000

#define CoringNeutral 1625

//int x = 0 ;


float gr1,gr2,gr3,gr4,gr5;
float gy1,gy2,gy3,gy4,gy5;
float gx1,gx2,gx3,gx4,gx5;


int dropflag;
int revflag;

int ch1,ch2,ch3,ch4,ch5,ch6;
int TXch1,TXch2,TXch3,TXch4,TXch5,TXch6;

int timcount,gdefspeed,gdefgainX, gdefgainY,gdefgainZ,gpull_duration;
int ackstartL,ackstart2L,ackcurL,ackangleL,ackdurL,ackflgL,ackstartR,ackstart2R,ackcurR,ackangleR,ackdurR,ackflgR;
 
 


void setup() {
int i;
     Wire.begin();        // join i2c bus (address optional for master)
   Serial.begin(115200);  // start serial for output
   timcount = 0;
   pinMode(LED_BUILTIN,  OUTPUT);


  Motor11.attach(3);  // Coring Motor
  Motor11.writeMicroseconds(CoringNeutral);

  for(i=0;i<10;i++)
     readArduSlave();


   sendArduSlaveCMD(0x0a,1501,0); // Tx Direct Bypass
 //   sendArduSlaveCMD(0x0a,1500,0); // Tx Direct 
 //   sendArduSlaveCMD(0,1501,1);  // Raw Mode
   sendArduSlaveCMD(0,1500,1);  // Non Raw
   sendArduSlaveCMD(0x0f,1500,0);  /// Send a Arduino Slave commmand to push all TX data to the Master Arduino
   sendArduSlaveCMD(5,1500,1);



  dropflag = 0;
  revflag = 0;
  gdefspeed = 0;
  gdefgainX = DEFGAIN;
  gdefgainY = DEFGAIN;
  gdefgainZ = DEFGAIN;

  gpull_duration = DEFDURATION;

  ackstartL = 0;
  ackstart2L = 0;
  ackcurL =0;
  ackangleL = 0;
  ackdurL = 0;
  ackflgL = 0;

  ackstartR = 0;
  ackstart2R = 0;
  ackcurR =0;
  ackangleR = 0;
  ackdurR = 0;
  ackflgR = 0;
 
 
  sendArduSlaveCMD(3,AtMid,0);
  sendArduSlaveCMD(6,AtMid,0);
  

  // Try to initialize the MPU6050
  
  if (!mpu.begin()) {
    Serial.println("Failed to find MPU6050 chip");
    while (1) {
      delay(10);
    }
  }



  delay(100);
  
  mpu.setAccelerometerRange(MPU6050_RANGE_8_G);
  mpu.setGyroRange(MPU6050_RANGE_500_DEG);
  mpu.setFilterBandwidth(MPU6050_BAND_21_HZ);

  delay(100);

  gr1=0;gr2=0;gr3=0;gr4=0;gr5=0;
  gy1=0;gy2=0;gy3=0;gy4=0;gy5=0;
  gx1=0;gx2=0;gx3=0;gx4=0;gx5=0;

  ch1 = 1500;ch2 = 1500;ch3 = 1000;ch4 = 1500;ch5 = 1500;ch6 = 1500;
  TXch1 = 1500;TXch2 = 1500;TXch3 = 1000;TXch4 = 1500;TXch5 = 0;TXch6 = 0;

  if (!bleSerial.beginAndSetupBLE("PERSE_MARS")) {
      Serial.println("failed to initialize HardwareBLESerial!");
      delay(1000);
    }
  
  ITimer.attachInterruptInterval(HW_TIMER_INTERVAL_MS * 100, TimerHandler);
  ISR_Timer.setInterval(TIMER_INTERVAL_100mS, UpdateCounter);
} 

void loop() {

sensors_event_t a, g, temp;
int chan, chanval,val, i;
unsigned char c1, c2;
unsigned char c;


   val = readArduSlave();
   c2 = val >> 8;
   c1 = val & 0xff;
   chan = (c2 & 0xF0) >> 4;
   chanval = ((c2 & 0x07)<<8) + c1;


   switch(chan)
   {
     case 1 :     
                ch1 = chanval;
                sendArduSlaveCMD(1,ch1,0);
                break;
     case 2 : 
                ch2 = chanval;break;
     case 3 :
                ch3 = chanval;
                sendArduSlaveCMD(3,ch3,0);
                break;
     case 4 :
                ch4 = chanval;
                sendArduSlaveCMD(4,ch4,0);
                break;
     case 5 : 
                ch5 = chanval;
                TXch5 = ch5 - AtStart;
                break;
     case 6 :  
                ch6 = chanval;
                TXch6 = ch6 - AtStart;
                break;
     default:
                break;
    
   }


  if (TXch5 == 0)
  {
    sendArduSlaveCMD(2,ch2,0);

    dropflag = 0;
    revflag = 0;   
  }
  else
  {

     mpu.getEvent(&a, &g, &temp);

     gr1=gr2;gr2=gr3;gr3=gr4;gr4=gr5;
     gy1=gy2;gy2=gy3;gy3=gy4;gy4=gy5;

     gr5 = abs(g.gyro.z*800);
     gy5 = abs(g.gyro.y*400);

     if ((((gr1+gr2+gr3+gr4+gr5)/5) > TXch6) || (((gy1+gy2+gy3+gy4+gy5)/5) > TXch6))
     {
        dropflag = 1;
        sendArduSlaveCMD(2,AtMid,0);

        if (revflag == 0)
        {
            sendArduSlaveCMD(2,AtMid - TXch5,0);
            delay(1000);
            sendArduSlaveCMD(2,AtMid,0);
            revflag = 1;        
        }
        
     }

     if (dropflag == 0)
     {   
            sendArduSlaveCMD(2,AtMid + TXch5,0);
     }

  }

  bleSerial.poll();
  while (bleSerial.available() > 0) {
    c = bleSerial.read();

    switch(c)
    {
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

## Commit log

2023-10-23 Add files via upload
    Initial upload of Arduino Codes
2023-10-23 Add files via upload
    Initial Upload
    [INGE_DEP_V2_SERVO_MAG.stl, INGE_DEP_V2_SERVO_MAG2.stl, ardu_mount.stl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]
2023-10-23 Update README.md
    Sensor details
2023-10-23 Update README.md
    added I2c details
2023-10-23 Update README.md
    Added Servo Details
2023-10-23 Update README.md
    servo mount 3d printed
2023-10-23 Update README.md
    added platform mount details
2023-10-23 Add files via upload
    Steering servo details
2023-10-23 Update README.md
    chassis box
2023-10-23 Add files via upload
    Added Servo and Ingenuity Helicopter Deployment demo video
2023-10-24 Update README.md
    sensor description added
2023-10-24 Update README.md
    LIDAR Address assignment via reset line
